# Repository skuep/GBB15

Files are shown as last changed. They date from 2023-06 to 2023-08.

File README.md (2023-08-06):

# GBB15
A gantry-mounted CAN stepper driver board for 15mm aluminum beams (mostly for PrintersForAnts printers). 

This board can be used e.g. for the Micron to have A/B motor controllers directly at the gantry. This reduces the number of wires required to be routed to the gantry.

Additionally, this board can be used for Voron-0 or Tridents as a USB to CAN converter (using the Klipper CAN bridge option) with **included** A/B motor controllers.

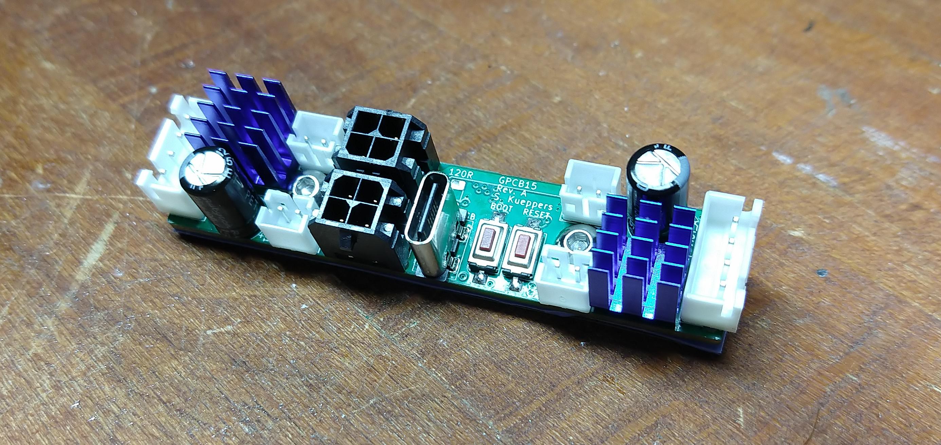
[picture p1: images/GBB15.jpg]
GBB15 Photo


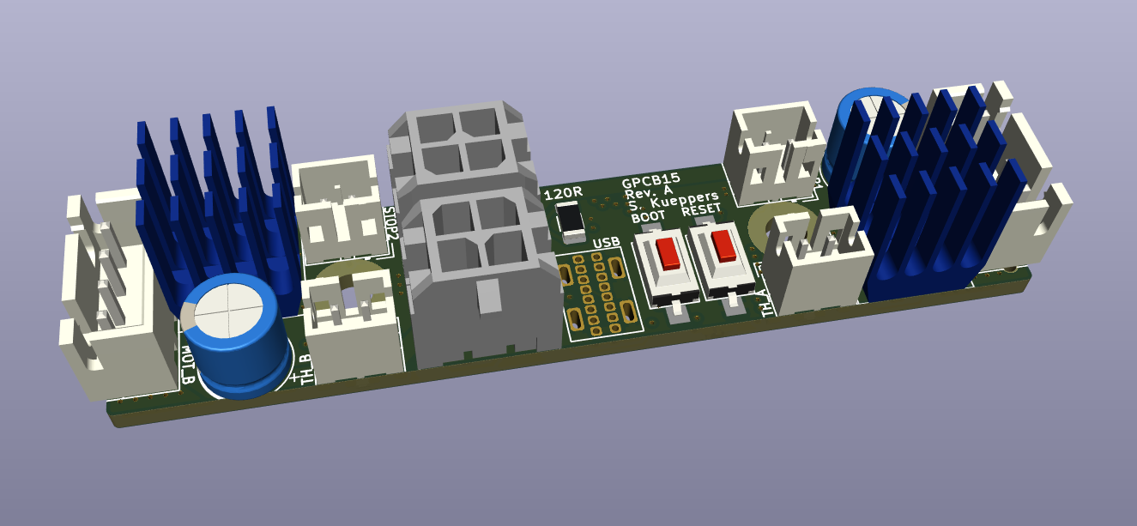
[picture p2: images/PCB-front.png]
PCB front side

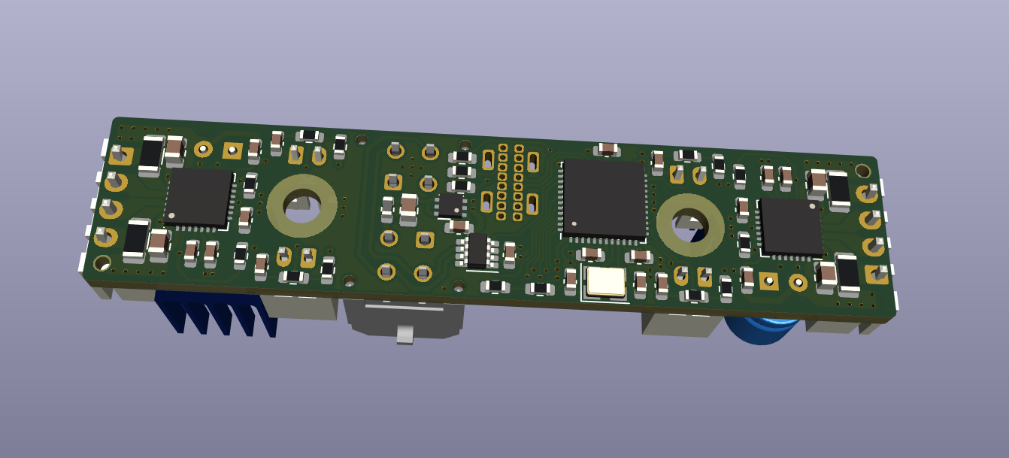
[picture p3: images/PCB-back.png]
PCB back side

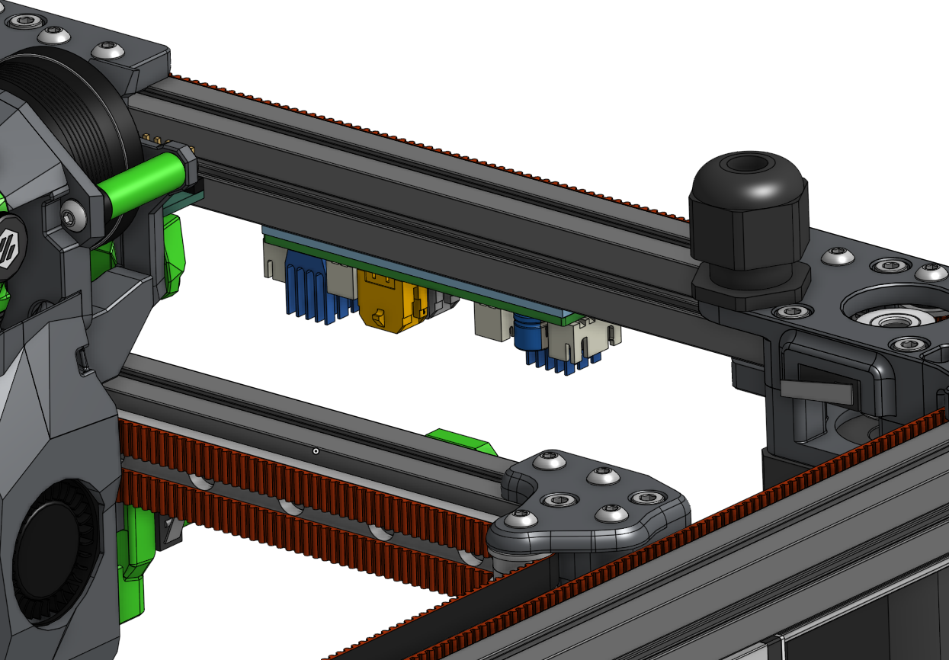
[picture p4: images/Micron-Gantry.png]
Micron Gantry


# JLCPCB Specifications
0. Upload ``GERBER-GBB15.zip``
1. Select Qty
2. PCB Thickness 1.6mm
3. LeadFree HASL
4. Enable PCB Assembly
5. Choose **Economic**
6. Select Assembly Side **Bottom Side**
7. Tooling holes: **Added by Customer**
8. Press **Confirm**
9. Upload ``BOM-GBB15.csv``and ``CPL-GBB15.csv``
10. Check that all parts are in stock and click **NEXT**
11. Look for odd placement in the preview, select **NEXT**

# Additionally needed LCSC parts
You can order these on LCSC

| Part | Quantity | Notes  | LCSC Part Number | Link  | 
| --- | :-: | --- | --- |--- |
| 100u/35V/105°C capacitor | 2 | | C3035369 | https://www.lcsc.com/product-detail/Aluminum-Electrolytic-Capacitors-Leaded_Rubycon-35YXJ100MFFCT1-6-3X11_C3035369.html |
| MicroFit 3.0 connector | 2 | Tin or Gold | C277721 or C563821 | https://www.lcsc.com/product-detail/Wire-To-Board-Wire-To-Wire-Connector_MOLEX-430450412_C277721.html or https://www.lcsc.com/product-detail/Pre-ordered-Connectors_MOLEX-430450413_C563821.html |
| JST PH 2.0mm 2-Pin conn. | 4 | Endstop/Thermistors | C131337 | https://www.lcsc.com/product-detail/Wire-To-Board-Wire-To-Wire-Connector_JST-Sales-America-B2B-PH-K-S-LF-SN_C131337.html |
| JST XH 2.5mm 4-Pin conn. | 2 | Steppers | C144395 | https://www.lcsc.com/product-detail/Wire-To-Board-Wire-To-Wire-Connector_JST-Sales-America-B4B-XH-A-LF-SN_C144395.html |
| Vertical THT USB-C conn. | 1 | | C3151747 | https://www.lcsc.com/product-detail/USB-Connectors_SHOU-HAN-TYPE-C-16PLC-H10-0_C3151747.html |
| CAN termination resistor | 1 | Optional! | C17909 | https://www.lcsc.com/product-detail/Chip-Resistor-Surface-Mount_UNI-ROYAL-Uniroyal-Elec-1206W4F1200T5E_C17909.html |
| Tactile Switches | 2 | Boot/Reset  | C255802 | https://www.lcsc.com/product-detail/Tactile-Switches_HYP-Hongyuan-Precision-1TS002E-2500-2501-CT_C255802.html |
| Heat Sink | 2 | Standard TMC2209 heatsink | C5250902 or C5250879 | https://www.lcsc.com/product-detail/Heat-sink-heatsink_wenhaoyongshun-D11-01-02_C5250902.html or https://www.lcsc.com/product-detail/Heat-sink-heatsink_wenhaoyongshun-F12-04-05_C5250879.html |
| 1.5mm M.2 Thermal pad | 1 | Cut to size 67x15mm | -- | https://www.amazon.de/-/en/Assorted-Thickness-Conductive-Silicone-Conductivity/dp/B07X38254H (DE) or https://www.amazon.com/ADWITS-12-Pack-Conductive-Silicone-Conductivity/dp/B07X81PRK7 (US) |

# Quick Guide
1. Solder top components (order: 120R resistor (if required), switches, 4x JST PH 2.0mm, 2x JST XH2.5mm, 2x MicroFit 3.0 2x2, USB connector, Capacitors & attach heatsinks)
1. Attach 1.5mm heat gap filler pad to bottom, cut to size if required using a sharp knife
1. Poke screw holes into the gap filler pads
1. Use M3x8mm screws to attach to bottom of gantry frame (see above)

Note that thermal connection to the 15mm beam is required! Otherwise the Stepper motor controllers might overheat.

# Firmware
1.  Plug in USB cable and connect 24V power, the green LED on the bottom side (Rev. B and up) must light up.
    Hold BOOT pushbutton, while tapping the RESET pushbutton and release all buttons. This is the sequence to set the GBB15 into DFU mode.

    **IMPORTANT**: STMicro decided on the entire STM32G0 series to set the ``nBOOT_SEL`` option bit and thus disable the ``BOOT0`` pin by default.
    This means you would have only one shot at uploading a bootloader, while the flash is empty. If you choose to re-program the bootloader (e.g. other CAN speed), you cannot get into the DFU mode anymore.
    For enabling the "legacy" ``BOOT0`` pin functionality, you have two options.
    1. You can use STMicro's STM32CubeProgrammer software to disable the ``nBOOT_SEL`` option bit by following the screenshot [here](doc/BOOT0-Via-STM32CubeProgrammer.png).
    1. Or if you prefer ``dfu-util``, which is included (or easily installed) in major linux distros (e.g. Raspberry Pi OS), you can run the ``enable_boot.hex`` firmware from [here](https://github.com/olikraus/stm32g031/tree/main/enable_boot0). 
       It will clear the ``nBOOT_SEL`` option bit from within the firmware, if it is not yet cleared.
       Use the following commands to upload the file.
       ```` 
           objcopy --input-target=ihex --output-target=binary enable_boot0.hex enable_boot0.bin # Convert hex to binary
           sudo dfu-util -a 0 -d 0483:df11 --dfuse-address 0x08000000:leave -D enable_boot0.bin
       ````
       After waiting for a second, the ``BOOT0`` pin is now enabled again and you can continue normally. 

       **NOTE:** Before continuing, remember to set the GBB15 into DFU mode again using the BOOT/RESET pushbuttons (see above).

1.  Build CanBoot according the instructions on the [CanBoot](https://github.com/Arksine/katapult) github page. 
    See [this](doc/GBB15-CanBoot.png) image for CanBoot menuconfig settings to use.

1.  Build the Klipper firmware according to the instructions on the [Klipper](https://www.klipper3d.org/Installation.html#building-and-flashing-the-micro-controller) github page.
    See [this](doc/GBB15-klipper.png) image for Klipper menuconfig settings to use.

1.  Upload CanBoot to the GBB15 using either STM32CubeProgrammer (if you have it installed) or using ``dfu-util`` with these commands.
    ````
        sudo dfu-util -a 0 -d 0483:df11 --dfuse-address 0x08000000:leave -D out/canboot.bin
    ````
    The device is now booted into CanBoot mode and can be accessed using the CanBoot tools.

1.  Upload the Klipper firmware to the GBB15 using either CanBoot's ``flashtool.py`` as described [here](https://github.com/Arksine/katapult#uploading-klipper) or Klipper's ``make flash`` (uses ``dfu-util``).
    1.  Using ``flashtool.py`` via CAN. Run these commands from the ``CanBoot/scripts`` directory
        ````
            python3 flashtool.py -i can0 -q # Check the UUID of the GBB15 board
            python3 flashtool.py -i can0 -f ~/klipper/out/klipper.bin -u <uuid> # Insert UUID here
        ````
    1.  Using ``make flash`` via Klipper Makefile. Run this command from the ``klipper`` directory.

        **NOTE:** For this, you need to set the GBB15 into DFU mode again using the BOOT/RESET pushbuttons (see above).
        ````
            make flash FLASH_DEVICE=0483:df11
        ````

# Pinout
This image shows the pinout of the GBB15 PCB. The CAN connector layout is compatible to the BigTreeTech EBB36 board (among others).
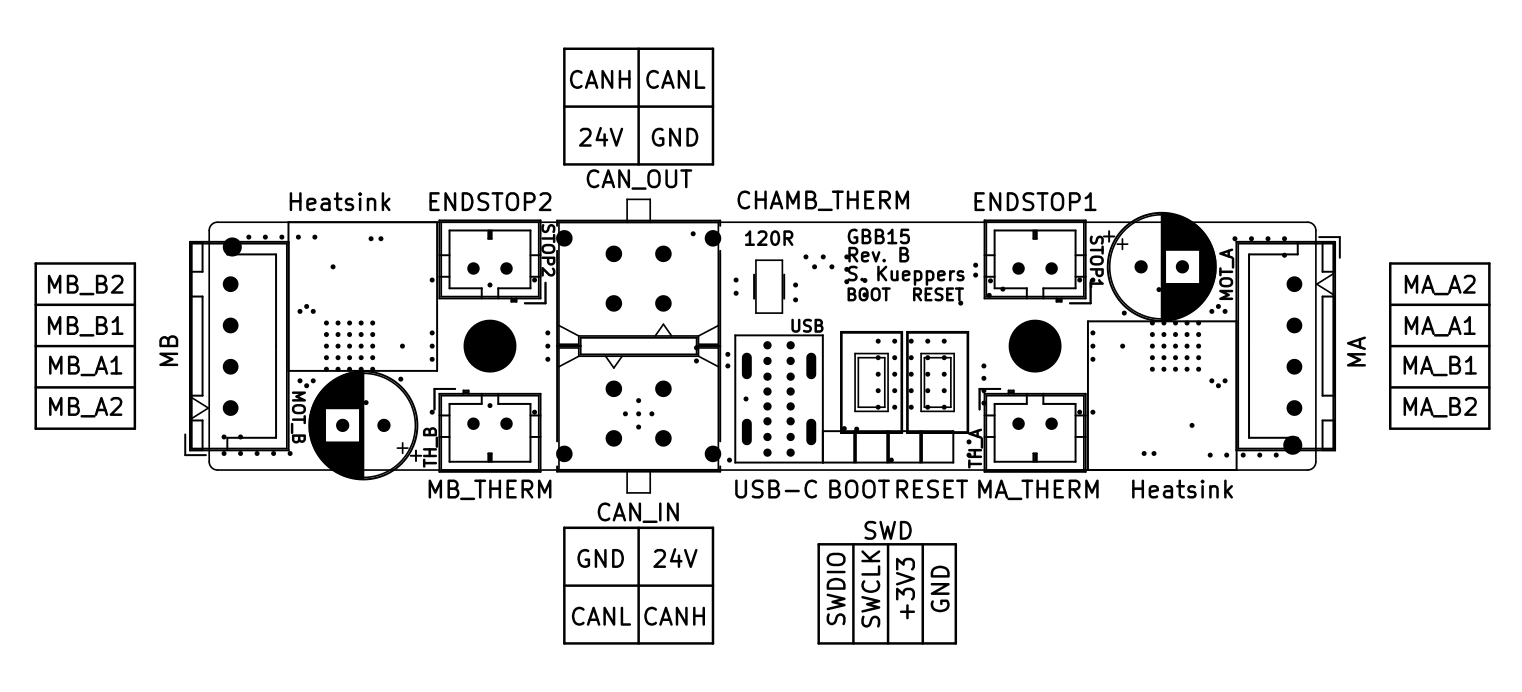
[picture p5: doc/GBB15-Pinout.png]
GBB15 Pinout


# Klipper configuration
````
[mcu gantry_mcu]
canbus_interface: can0
canbus_uuid: f7b6d9f26b4a

...

[temperature_sensor chamber]
sensor_type: Generic 3950
sensor_pin: gantry_mcu:PA1 # SMD thermistor on GBB15 PCB
#sensor_pin: gantry_mcu:PA3 # Alternatively, this is STOP1 connector if it is not used otherwise
#sensor_pin: gantry_mcu:PA2 # Alternatively, this is STOP2 connector if it is not used otherwise (for Rev. B and up) 
pullup_resistor: 4700

[temperature_sensor Motor_A]
sensor_type: Generic 3950
sensor_pin: gantry_mcu:PB11 # TH_A on GBB15 PCB
pullup_resistor: 4700

[temperature_sensor Motor_B]
sensor_type: Generic 3950
sensor_pin: gantry_mcu:PB12 # TH_B on GBB15 PCB
pullup_resistor: 4700

[temperature_sensor gantry_temp]
sensor_type: temperature_mcu
sensor_mcu: gantry_mcu
min_temp: 0
max_temp: 100

...

[stepper_y]
step_pin: gantry_mcu:PB2
dir_pin: gantry_mcu:PB1
enable_pin: !gantry_mcu:PB13
endstop_pin: gantry_mcu:PA3 # This is the STOP1 connector on GBB15 PCB
#endstop_pin: gantry_mcu:PA2 # Alternatively, this is STOP2 connector (for Rev. B and up, PC13 on Rev. A)
#endstop_pin: gantry_mcu:PB0 # This is the DIAG pin of the TMC driver for sensorless homing
...

[tmc2209 stepper_y]
uart_pin: gantry_mcu:PA4
sense_resistor: 0.110
...

[stepper_x]
step_pin: gantry_mcu:PB7
dir_pin: gantry_mcu:PB8
enable_pin: !gantry_mcu:PB9
endstop_pin: gantry_mcu:PA2 # This is STOP2 connector (for Rev. B and up, PC13 on Rev. A)
#endstop_pin: gantry_mcu:PA3 # Alternatively, this is the STOP1 connector on GBB15 PCB
#endstop_pin: gantry_mcu:PB5 # This is the DIAG pin of the TMC driver for sensorless homing
...

[tmc2209 stepper_x]
uart_pin: gantry_mcu:PB3
sense_resistor: 0.110
...

````

"Chamber" thermistor in this configuration is a SMD thermistor on the PCB. It reads probably 15-20°C above the actual chamber temperature, when the stepper motors are enabled and running. 
- To get better chamber temp readings, you can use TH_A or TH_B to connect a remote thermistor (in case you don't need those for monitoring the motor temperatures). 
- Alternatively you can (mis-)use the STOP1 (All revisions) and STOP2 (Rev. B and up) pins for analog readings. Easiest is a through-hole 100K B3950 NTC crimped into a JST PH2.0 and connected to one of the mentioned header pins.

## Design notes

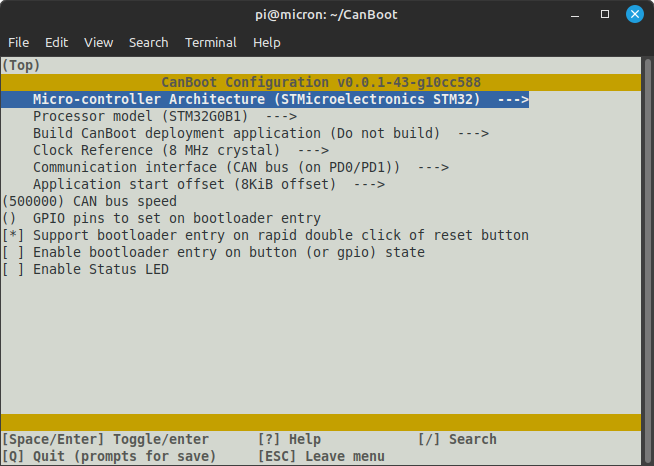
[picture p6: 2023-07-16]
doc/GBB15-CanBoot.png

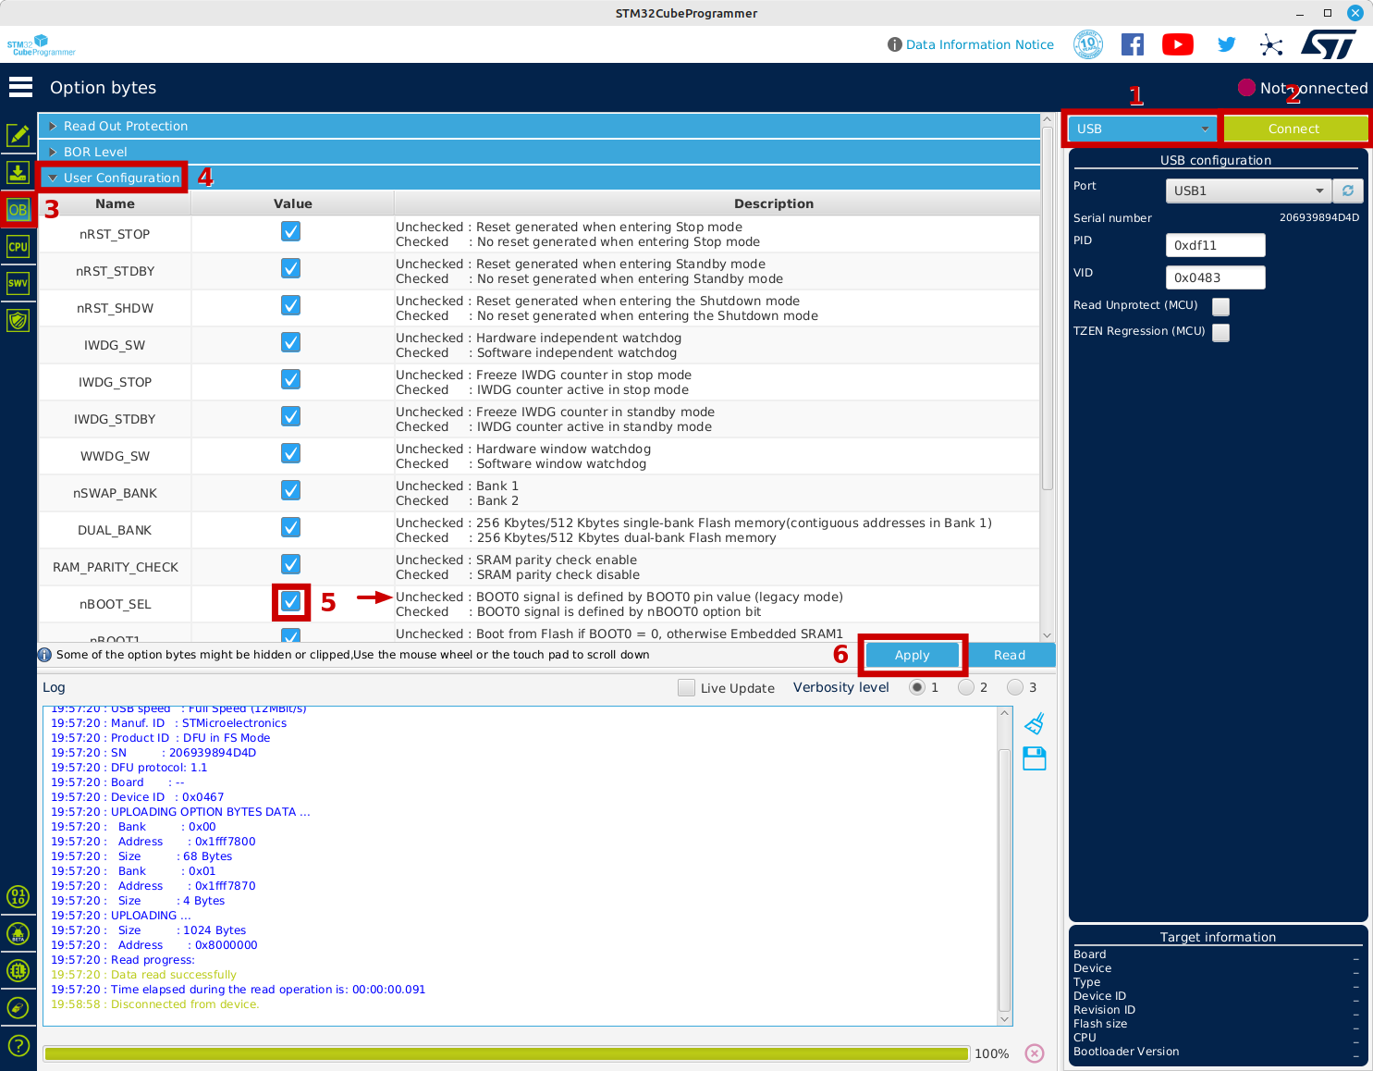
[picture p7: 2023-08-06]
doc/BOOT0-Via-STM32CubeProgrammer.png

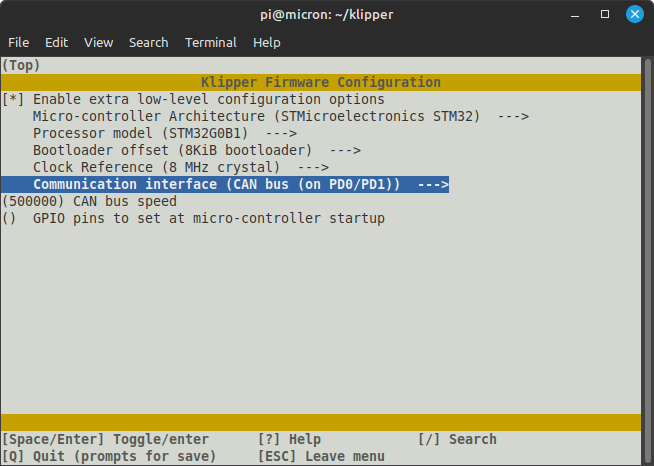
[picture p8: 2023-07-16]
doc/GBB15-klipper.png

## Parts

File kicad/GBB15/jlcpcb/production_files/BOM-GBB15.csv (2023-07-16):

Comment | Designator | Footprint | LCSC
600R@100MHz | FB1 | L_0603_1608Metric | C1002
MAX3051EKA+T | U4 | SOT-23-8 | C112005
MA_THERM | J3,J4,J7,J8 | JST_PH_B2B-PH-K_1x02_P2.00mm_Vertical | C131337
MA | J5,J6 | JST_XH_B4B-XH-A_1x04_P2.50mm_Vertical | C144395
100n/X5R/50V | C11,C16,C18,C2,C21,C24,C26,C27,C28,C6,C7 | C_0603_1608Metric | C14663
22p/NP0 | C3,C4 | C_0603_1608Metric | C1653
N.M. (120R) | R19 | R_1206_3216Metric | C17909
4.7u/X5R/10V | C10,C14,C22,C30 | C_0603_1608Metric | C19666
22n/X5R/50V | C13,C5 | C_0603_1608Metric | C21122
4.7K | R11,R12,R14,R17,R20,R21,R22,R23,R5,R6 | R_0603_1608Metric | C23162
5.1K | R13,R15 | R_0603_1608Metric | C23186
BOOT | SW1,SW2 | SW_SPST_CK_RS282G05A3 | C255802
10K | R16,R3,R4,R7,R8 | R_0603_1608Metric | C25804
Crystal_GND24 | Y1 | Crystal_SMD_3225-4Pin_3.2x2.5mm | C2682774
STM32G0B1CEU6 | U2 | QFN-48-1EP_7x7mm_P0.5mm_EP5.6x5.6mm | C2829190
1u/X5R/50V | C12,C15,C29,C8,C9 | C_0805_2012Metric | C28323
0R11 | R1,R10,R2,R9 | R_1206_3216Metric | C2934288
100u/35V/105°C | C1,C17 | CP_Radial_D6.3mm_P2.50mm | C3035369
USB-C | J10 | TYPE-C 16PLC-H10.0 | C3151747
TMC2209-LA-T | U1,U3 | QFN-28-1EP_5x5mm_P0.5mm_EP3.35x3.35mm | C465949
CAN_IN | J1,J2 | Molex_Micro-Fit_3.0_43045-0412_2x02_P3.00mm_Vertical | C563821
LED | D1 | LED_0603_1608Metric | C72043
NCP730BMT330TBG | U5 | DFN-6-1EP_2x2mm_P0.65mm_EP1x1.6mm | C892821
Thermistor | TH1 | R_0603_1608Metric | C919169
MountingHole | H2 | MountingHole_3.2mm_M3
MountingHole | H1 | MountingHole_3.2mm_M3
Heatsink | HS2 | TMC2209-Heatsink
Heatsink | HS1 | TMC2209-Heatsink
Fiducial | FID1 | TOOLING-HOLE
Fiducial | FID2 | TOOLING-HOLE
TestPoint | TP2 | TestPoint_Pad_1.5x1.5mm
TestPoint | TP1 | TestPoint_Pad_1.5x1.5mm

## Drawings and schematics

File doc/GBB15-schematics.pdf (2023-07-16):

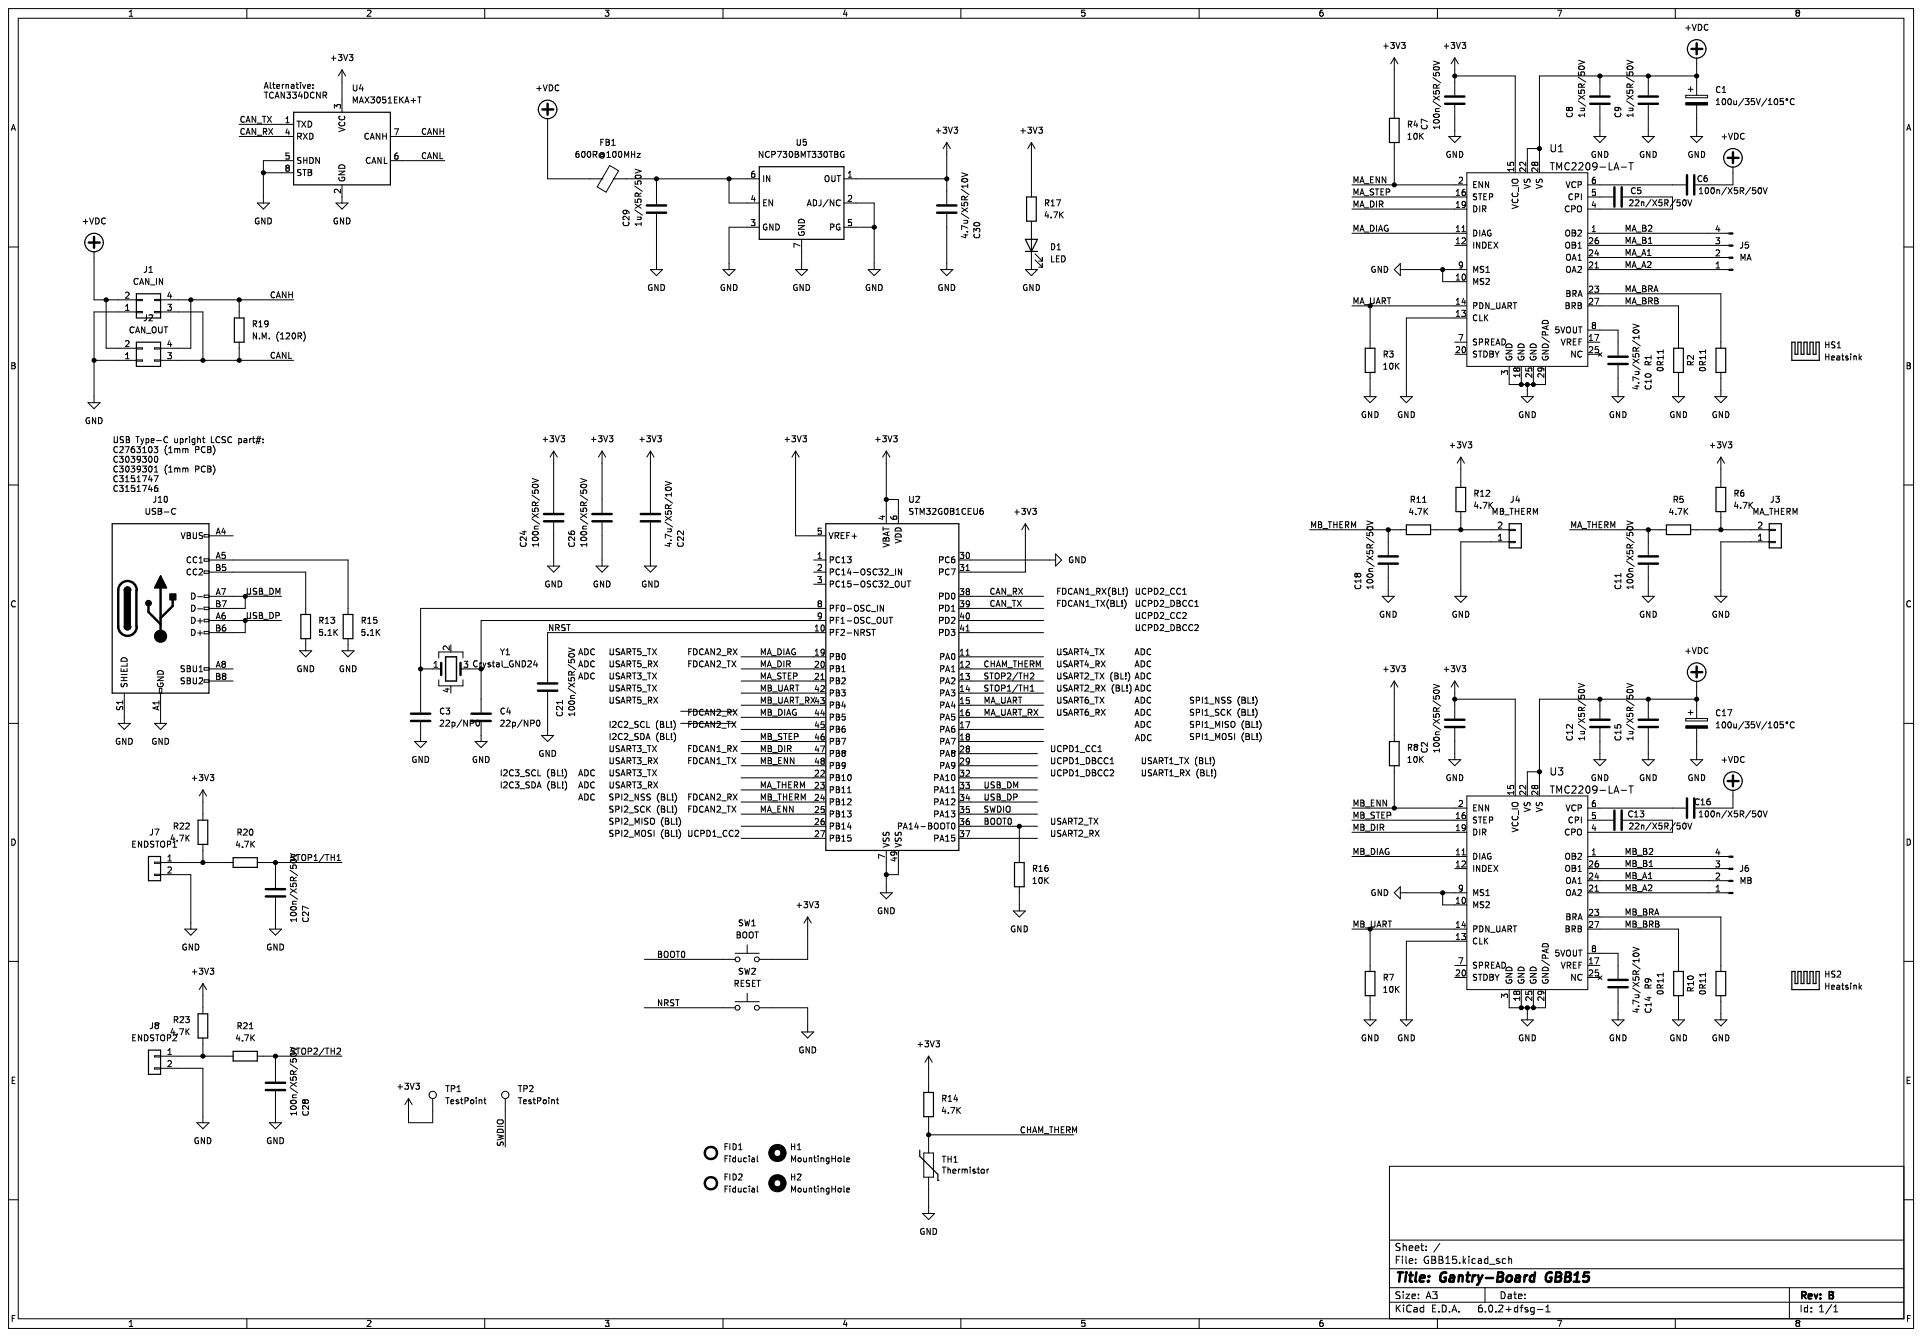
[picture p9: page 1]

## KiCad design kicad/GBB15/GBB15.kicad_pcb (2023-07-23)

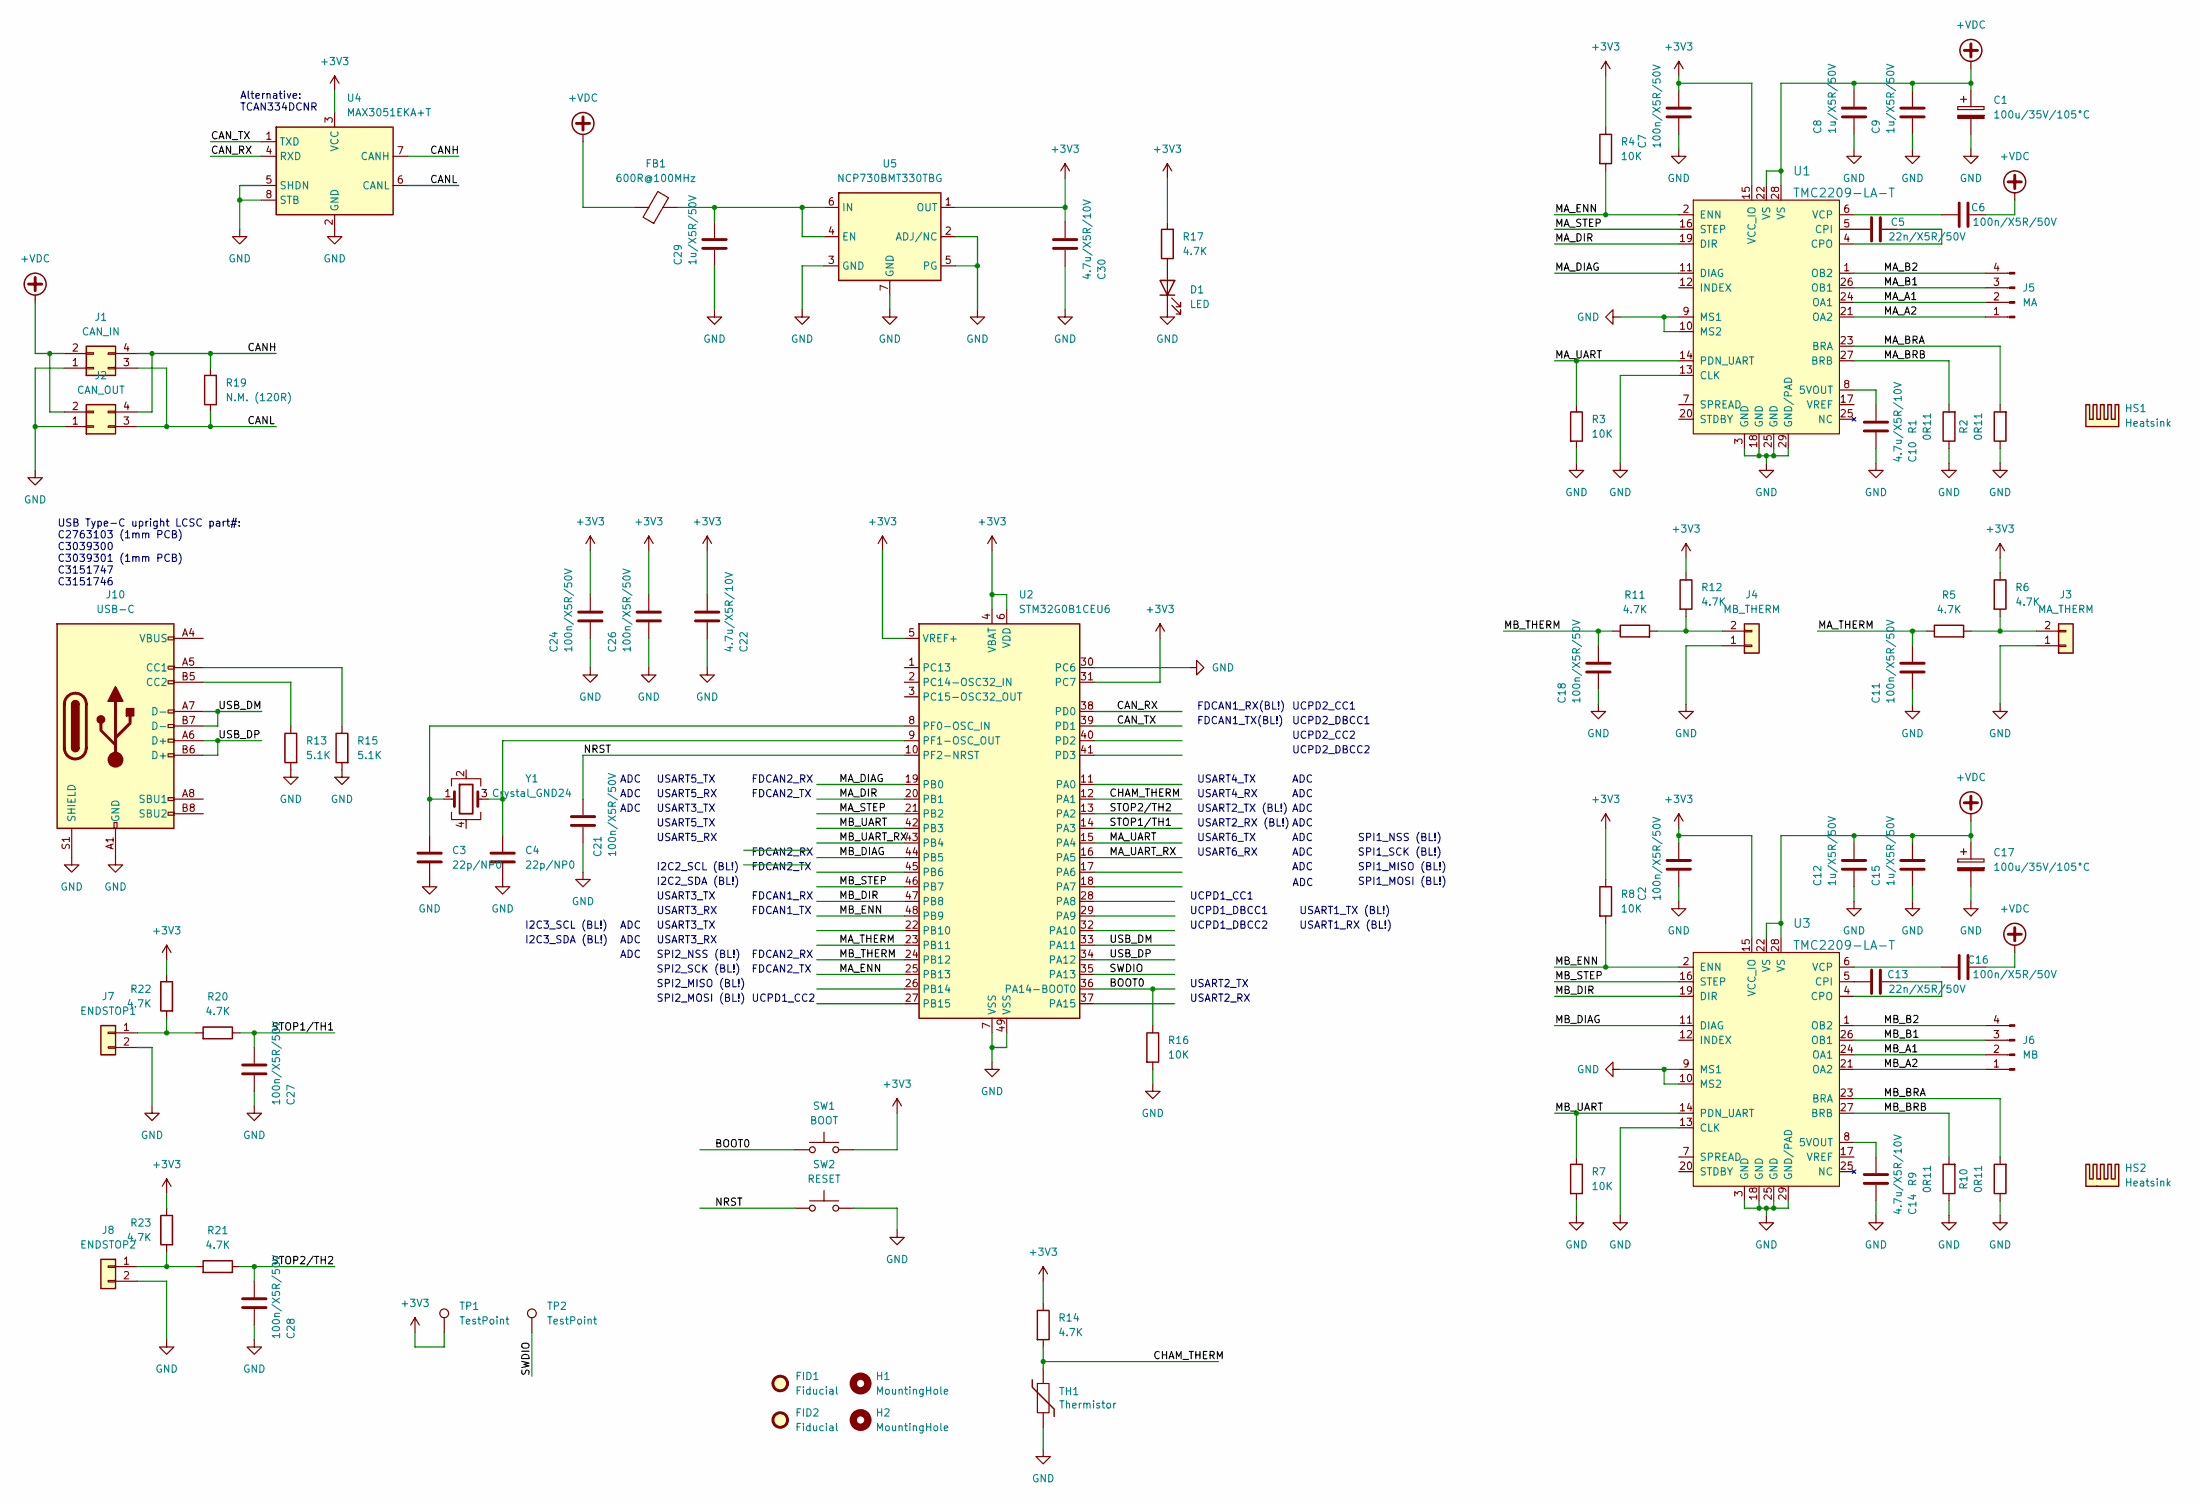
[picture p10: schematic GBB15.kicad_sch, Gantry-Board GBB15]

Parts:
C1, C17: 100u/35V/105°C; CP_Radial_D6.3mm_P2.50mm; LCSC C3035369
C2, C6, C7, C11, C16, C18, C21, C24, C26, C27, C28: 100n/X5R/50V; C_0603_1608Metric; LCSC C14663
C3, C4: 22p/NP0; C_0603_1608Metric; LCSC C1653
C5, C13: 22n/X5R/50V; C_0603_1608Metric; LCSC C21122
C8, C9, C12, C15, C29: 1u/X5R/50V; C_0805_2012Metric; LCSC C28323
C10, C14, C22, C30: 4.7u/X5R/10V; C_0603_1608Metric; LCSC C19666
D1: LED; LED_0603_1608Metric; LCSC C72043
FB1: 600R@100MHz; L_0603_1608Metric; LCSC C1002
FID1, FID2: Fiducial; TOOLING-HOLE
H1, H2: MountingHole; MountingHole_3.2mm_M3
HS1, HS2: Heatsink; TMC2209-Heatsink
J1: CAN_IN; Molex_Micro-Fit_3.0_43045-0412_2x02_P3.00mm_Vertical; LCSC C563821
J2: CAN_OUT; Molex_Micro-Fit_3.0_43045-0412_2x02_P3.00mm_Vertical; LCSC C563821
J3: MA_THERM; JST_PH_B2B-PH-K_1x02_P2.00mm_Vertical; LCSC C131337
J4: MB_THERM; JST_PH_B2B-PH-K_1x02_P2.00mm_Vertical; LCSC C131337
J5: MA; JST_XH_B4B-XH-A_1x04_P2.50mm_Vertical; LCSC C144395
J6: MB; JST_XH_B4B-XH-A_1x04_P2.50mm_Vertical; LCSC C144395
J7: ENDSTOP1; JST_PH_B2B-PH-K_1x02_P2.00mm_Vertical; LCSC C131337
J8: ENDSTOP2; JST_PH_B2B-PH-K_1x02_P2.00mm_Vertical; LCSC C131337
J10: USB-C; TYPE-C 16PLC-H10.0; LCSC C3151747
R1, R2, R9, R10: 0R11; R_1206_3216Metric; LCSC C2934288
R3, R4, R7, R8, R16: 10K; R_0603_1608Metric; LCSC C25804
R5, R6, R11, R12, R14, R17, R20, R21, R22, R23: 4.7K; R_0603_1608Metric; LCSC C23162
R13, R15: 5.1K; R_0603_1608Metric; LCSC C23186
R19: N.M. (120R); R_1206_3216Metric; LCSC C17909
SW1: BOOT; SW_SPST_CK_RS282G05A3; LCSC C255802
SW2: RESET; SW_SPST_CK_RS282G05A3; LCSC C255802
TH1: Thermistor; R_0603_1608Metric; LCSC C919169
TP1, TP2: TestPoint; TestPoint_Pad_1.5x1.5mm
U1, U3: TMC2209-LA-T; QFN-28-1EP_5x5mm_P0.5mm_EP3.35x3.35mm; MPN TMC2209-LA-T; Digi-Key_PN 1460-1398-2-ND
U2: STM32G0B1CEU6; QFN-48-1EP_7x7mm_P0.5mm_EP5.6x5.6mm; LCSC C2829190
U4: MAX3051EKA+T; SOT-23-8; LCSC C112005
U5: NCP730BMT330TBG; DFN-6-1EP_2x2mm_P0.65mm_EP1x1.6mm; LCSC C892821
Y1: Crystal_GND24; Crystal_SMD_3225-4Pin_3.2x2.5mm; LCSC C2682774

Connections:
+3V3: C2.2, C7.2, C22.2, C24.2, C26.2, C30.2, R4.1, R6.1, R8.1, R12.1, R14.1, R17.2, R22.1, R23.1, SW1.2, TP1.1, U1.15 (VCC_IO), U2.4 (VBAT), U2.5 (VREF+), U2.6 (VDD), U2.31 (PC7), U3.15 (VCC_IO), U4.3 (VCC), U5.1 (OUT)
+VDC: C1.1, C6.2, C8.2, C9.2, C12.2, C15.2, C16.2, C17.1, FB1.1, J1.2, J2.2, U1.22 (VS), U1.28 (VS), U3.22 (VS), U3.28 (VS)
/BOOT0: R16.1, SW1.1, U2.36 (PA14-BOOT0)
/CANH: J1.4, J2.4, R19.2, U4.7 (CANH)
/CANL: J1.3, J2.3, R19.1, U4.6 (CANL)
/CAN_RX: U2.38 (PD0), U4.4 (RXD)
/CAN_TX: U2.39 (PD1), U4.1 (TXD)
/CHAM_THERM: R14.2, TH1.1, U2.12 (PA1)
/MA_A1: J5.2, U1.24 (OA1)
/MA_A2: J5.1, U1.21 (OA2)
/MA_B1: J5.3, U1.26 (OB1)
/MA_B2: J5.4, U1.1 (OB2)
/MA_BRA: R2.2, U1.23 (BRA)
/MA_BRB: R1.2, U1.27 (BRB)
/MA_DIAG: U1.11 (DIAG), U2.19 (PB0)
/MA_DIR: U1.19 (DIR), U2.20 (PB1)
/MA_ENN: R4.2, U1.2 (ENN), U2.25 (PB13)
/MA_STEP: U1.16 (STEP), U2.21 (PB2)
/MA_THERM: C11.2, R5.1, U2.23 (PB11)
/MA_UART: R3.1, U1.14 (PDN_UART), U2.15 (PA4)
/MA_UART_RX: U2.16 (PA5)
/MB_A1: J6.2, U3.24 (OA1)
/MB_A2: J6.1, U3.21 (OA2)
/MB_B1: J6.3, U3.26 (OB1)
/MB_B2: J6.4, U3.1 (OB2)
/MB_BRA: R10.2, U3.23 (BRA)
/MB_BRB: R9.2, U3.27 (BRB)
/MB_DIAG: U2.44 (PB5), U3.11 (DIAG)
/MB_DIR: U2.47 (PB8), U3.19 (DIR)
/MB_ENN: R8.2, U2.48 (PB9), U3.2 (ENN)
/MB_STEP: U2.46 (PB7), U3.16 (STEP)
/MB_THERM: C18.2, R11.1, U2.24 (PB12)
/MB_UART: R7.1, U2.42 (PB3), U3.14 (PDN_UART)
/MB_UART_RX: U2.43 (PB4)
/NRST: C21.2, SW2.1, U2.10 (PF2-NRST)
/STOP1/TH1: C27.2, R20.1, U2.14 (PA3)
/STOP2/TH2: C28.2, R21.1, U2.13 (PA2)
/SWDIO: TP2.1, U2.35 (PA13)
/USB_DM: J10.A7 (D-), J10.B7 (D-), U2.33 (PA11)
/USB_DP: J10.A6 (D+), J10.B6 (D+), U2.34 (PA12)
GND: C1.2, C2.1, C3.1, C4.1, C7.1, C8.1, C9.1, C10.1, C11.1, C12.1, C14.1, C15.1, C17.2, C18.1, C21.1, C22.1, C24.1, C26.1, C27.1, C28.1, C29.1, C30.1, D1.1 (K), J1.1, J2.1, J3.1, J4.1, J7.2, J8.2, J10.A1 (GND), J10.A12 (GND), J10.B1 (GND), J10.B12 (GND), J10.S1 (SHIELD), R1.1, R2.1, R3.2, R7.2, R9.1, R10.1, R13.2, R15.2, R16.2, SW2.2, TH1.2, U1.3 (GND), U1.9 (MS1), U1.10 (MS2), U1.13 (CLK), U1.18 (GND), U1.25 (GND), U1.29 (GND/PAD), U2.7 (VSS), U2.30 (PC6), U2.49 (VSS), U3.3 (GND), U3.9 (MS1), U3.10 (MS2), U3.13 (CLK), U3.18 (GND), U3.25 (GND), U3.29 (GND/PAD), U4.2 (GND), U4.5 (SHDN), U4.8 (STB), U5.2 (ADJ/NC), U5.3 (GND), U5.5 (PG), U5.7 (GND)
unnamed: C3.2, U2.8 (PF0-OSC_IN), Y1.1
unnamed: C4.2, U2.9 (PF1-OSC_OUT), Y1.3
unnamed: C5.1, U1.4 (CPO)
unnamed: C5.2, U1.5 (CPI)
unnamed: C6.1, U1.6 (VCP)
unnamed: C10.2, U1.8 (5VOUT)
unnamed: C13.1, U3.4 (CPO)
unnamed: C13.2, U3.5 (CPI)
unnamed: C14.2, U3.8 (5VOUT)
unnamed: C16.1, U3.6 (VCP)
unnamed: C29.2, FB1.2, U5.4 (EN), U5.6 (IN)
unnamed: D1.2 (A), R17.1
unnamed: J3.2, R5.2, R6.2
unnamed: J4.2, R11.2, R12.2
unnamed: J7.1, R20.2, R22.2
unnamed: J8.1, R21.2, R23.2
unnamed: J10.A4 (VBUS), J10.A9 (VBUS), J10.B4 (VBUS), J10.B9 (VBUS)
unnamed: J10.A5 (CC1), R15.1
unnamed: J10.B5 (CC2), R13.1

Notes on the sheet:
SPI2_MOSI (BL!)
USART5_RX
ADC
USART4_RX
UCPD2_DBCC1
Alternative: TCAN334DCNR
FDCAN2_RX
UCPD1_CC2
USART3_TX
USART4_TX
FDCAN2_TX
FDCAN1_RX
UCPD1_CC1
SPI1_SCK (BL!)
SPI2_MISO (BL!)
USART1_TX (BL!)
USART2_TX
I2C3_SDA (BL!)
USART2_TX (BL!)
USART5_TX
I2C3_SCL (BL!)
SPI1_MOSI (BL!)
SPI2_SCK (BL!)
FDCAN1_TX(BL!)
USART2_RX
USART3_RX
I2C2_SCL (BL!)
FDCAN1_RX(BL!)
FDCAN1_TX
USART2_RX (BL!)
USART1_RX (BL!)
SPI2_NSS (BL!)
USB Type-C upright LCSC part#: C2763103 (1mm PCB) C3039300 C3039301 (1mm PCB) C3151747 C3151746
USART6_RX
UCPD1_DBCC1
I2C2_SDA (BL!)
SPI1_NSS (BL!)
UCPD2_CC2
SPI1_MISO (BL!)
UCPD2_CC1

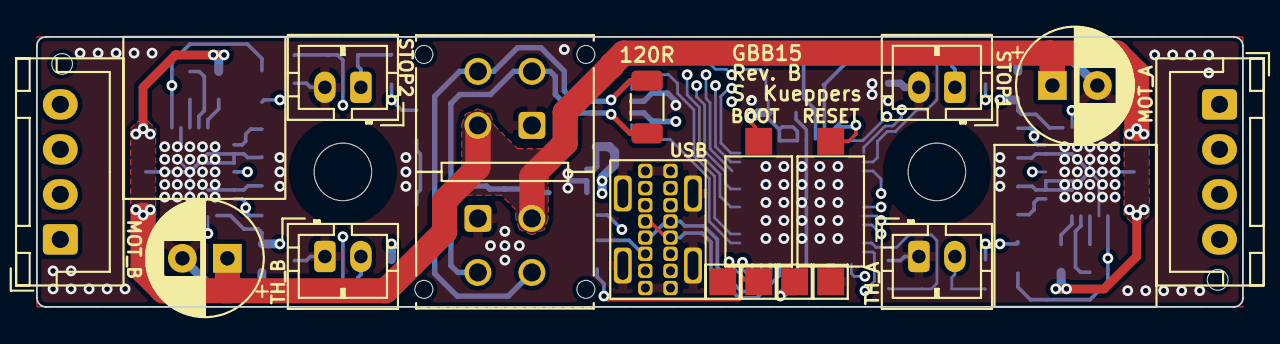
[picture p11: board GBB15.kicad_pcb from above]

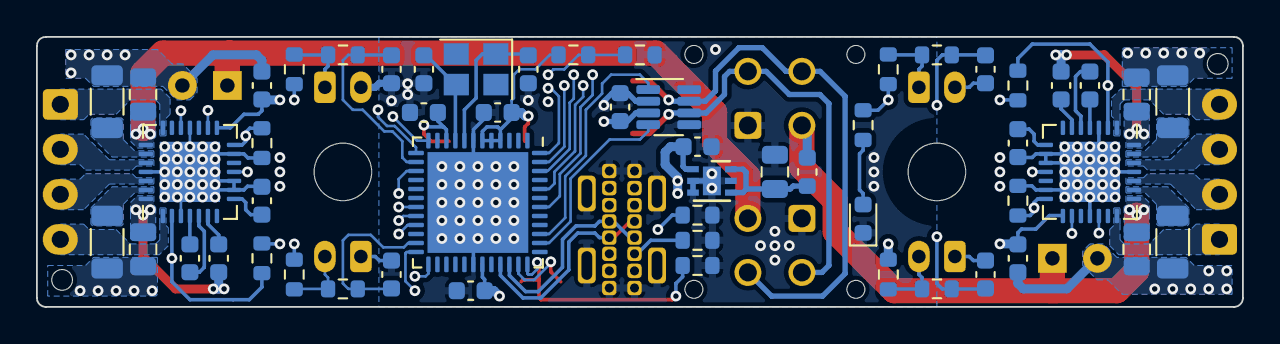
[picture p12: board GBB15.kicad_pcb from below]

Board: 4 copper layers, 67.0 x 15.0 mm, 76 parts (54 on the bottom side), 58 nets.

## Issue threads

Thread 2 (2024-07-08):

Couple quick questions

allenrowand, 2024-07-08:
No issues (yet), just questions:
1) Is there any reason why this couldn’t be used on a V2.4?
2) I want to confirm that if I want to use the CAN output I’d need to remove the 120 ohm resistor on the GBB and terminate at the toolhead

Thanks for your work, looking forward to installing this!

skuep, 2024-07-08:
Hi there,
1. It has been designed to fit into small form factors. You can use it with the V2.4 probably (maybe thermal contact to the extrusion is not as good, because of the larger slot width). Other than that there is no real reason against it.
2. Yes, if the 120R is assembled (it's not by default) and the GBB15 is not at one of the two ends of the busy you need to remove it.
🤞👍

allenrowand, 2024-07-08:
Thanks for the info. Maybe I’ll look into adding a plate between the GBB15 and 2020 to act as a heat spreader

skuep, 2024-07-08:
That might work.. I would suggest you just try without one first, and check the PCB temp using the Integrated thermistor.

Closed 2024-07-08.

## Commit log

2023-06-06 Work in progress, layout close to finish
    [Micron-Gantry-PCB.kicad_pcb, Micron-Gantry-PCB.kicad_sch]
2023-06-06 Corrected USB footprint, renamed some signals
    [Micron-Gantry-PCB.kicad_pcb, Micron-Gantry-PCB.kicad_sch]
2023-06-06 Renamed project to GBB15
    [GBB15.kicad_pcb, GBB15.kicad_sch]
2023-06-06 Minor touches
    [GBB15.kicad_pcb]
2023-06-06 PCB cleanup
    [GBB15.kicad_sch]
2023-06-07 Small changes in JST connector type
    [GBB15.kicad_pcb, GBB15.kicad_sch]
2023-06-07 Added LCSC properties in schematic
    [GBB15.kicad_sch]
2023-06-07 Connected unconnected pads on TCAN334 to ground
    [GBB15.kicad_pcb, GBB15.kicad_sch]
2023-06-07 Added JLCPCB production files
    [BOM-GBB15.csv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]
2023-06-07 Correct 100nF capacitor part number and changed to MAX3051 instead of TCAN334
    [BOM-GBB15.csv, GBB15.kicad_pcb, GBB15.kicad_sch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]
2023-06-07 Added tooling holes
    [BOM-GBB15.csv, GBB15.kicad_pcb, GBB15.kicad_sch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]
2023-06-07 Corrected rotations for ICs
    [CPL-GBB15.csv]
2023-06-07 Added rotation overrides file
    [rotations.csv]
2023-06-07 Added PCB images
2023-06-08 Changed silkscreen
    [GBB15.kicad_pcb]
2023-06-08 Added image of GBB15 mounted on Micron gantry
2023-06-25 Update README.md
    Added Klipper stuff
2023-06-27 Bumped revision to B, added Power LED and moved ENDSTOP2 to ADC pin
    [GBB15.kicad_pcb, GBB15.kicad_sch]
2023-07-16 Added pinout documentation on User.Drawings layer
    [GBB15.kicad_pcb, GBB15.kicad_sch]
2023-07-16 Added additional debug pads for SWD
    [GBB15.kicad_pcb, GBB15.kicad_sch]
2023-07-16 Increased connection width to MicroFit GND pads
    [GBB15.kicad_pcb]
2023-07-16 Updated production files
    [BOM-GBB15.csv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]
2023-07-16 Added schematics and canboot/klipper configs
2023-07-23 Minor trace changes
    [GBB15.kicad_pcb]
